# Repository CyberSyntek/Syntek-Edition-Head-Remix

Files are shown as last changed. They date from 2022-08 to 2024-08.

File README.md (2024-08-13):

Welcome to the Syntek Edition Head Remix!
=
TempMainSnip

UPDATES / NOTES
= 

Some of the information on this page is very outdated! I had originally designed the project to work with MG90D sized servos and a PCA9685, which was later changed to using the recommended setup as listed in the BOM. 

Due to the changes over time, the tutorials maybe a bit clunky in that respect as alot of the pictures used still include the old servos and PCA9685. Sorry about that. 

All the files you need are available though. :)

I'm currently using the JX Servo edit files of this head which will use the following servos to replace MG90D/MG92B. 

- x12 - JX PDI-1109

- x3 - JX PDI-1181

The PDI-1181 is a slightly larger servo so it will have more torque on all 3 jaw motors. The JX servos seem to be the quietest, no buzz and better performance servos out of the 7 different micro servos I bought and tested. They should really improve overall performance in general. 

I have left the files to use the previous old setup available also for those wishing to use MG90D/MG90S type servos.

I likely will not be updating this page further or do not have plans to do so at this point. I am planning on working on a more advanced silicone cast type head at some point in the future which is where the focus will be directed. 

ABOUT
=
On this page you will find all of the Syntek edition remixed head stl files, components needed, step by step put together tutorials and information relating to getting it running in myrobotlab (MRL). Future updates and files shall be available here as well. :)

As I am still early into the experimenting phase of this head also, I expect that there will be a number of updates to improve this page, files and write ups in the weeks to come. Stay tuned!

WHAT IS SYNTEK?
=
An introduction to Syntek (My InMoov Robot)

https://user-images.githubusercontent.com/81597534/182945941-7be97dca-e8e5-45d9-b666-c8eca6ea6b64.mp4

CURIOUS ABOUT INMOOV?
= 
If you were unfamiliar with InMoov robot and or are now more curious about it, you should head over to the InMoov website and find out more about the project  by clicking the image below as THIS project page is directly related to the InMoov project. 

<a href="https://www.inmoov.fr" />


WHAT IS THE SYNTEK EDITION REMIXED HEAD?
= 
It is a mostly magnetically held remixed edition of Gael Langevin (InMoov Founder)'s InMoov robot head that has been fit with independent eyes, eyelids, eyebrows and an additional axis in the jaw. This head is controlled via a PCA9685 micro controller, an Arduino Nano and MYROBOTLAB and can be built to function independently or as part of your InMoov robot. 

FIRST TIME USING A PCA9865 AND MYROBOTLAB?
=
No problem! Here is my "Beginners guide to moving servos with a PCA9685 and MYROBOTLAB" video to help you get started.

Beginners guide to moving servos with a PCA9685 and MYROBOTLAB (https://youtu.be/unIUJA24uBI  "Beginners guide to moving servos with a PCA9685 and MYROBOTLAB")

And while we are at it, here is a bonus link to the MYROBOTLAB (MRL) homepage: http://myrobotlab.org/

-BOM- 
=
For a full detailed list of the electronics, hardware and everything needed, please refer to BOM readme file. 

https://github.com/CyberSyntek/Syntek-Edition-Head-Remix/tree/main/BOM

TUTORIALS
= 
The tutorials begin here!

https://github.com/CyberSyntek/Syntek-Edition-Head-Remix/tree/main/01-MainPlate

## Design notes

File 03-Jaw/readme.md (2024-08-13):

JAW - STL FILES
=
JawFiles

WARNING: Some of the files may look different than the original tutorial as they have been updated and adjusted to meet other changes in the build so far. I will update the images to match the parts eventually. The put together is still the same, just slightly altered a few parts for better functionality.

- ServoConnector-JXedit.stl x2 - IF USING RECOMMENDED SERVOS FROM BOM, PRINT THIS!

- ServoConnectorV2 - x2  - If using the above, you do not need to print these. These were for original MG90D servo builds.

- BallLinkConnector

- Hinge-L

- Hinge-R

- HingeBase

- HingeCover

- HingeLink

- Jaw - (V2 Jaw modified to fit AdjustableInsert.stl from the skull page. 

ELECTRONICS
=

- x2 - JX PDI-1181 servos. (Lateral Jaw). 

SCREWS / BOLTS / CONNECTORS
=
- x4 - M2x8mm Screws 

- x4 - M2x12mm Screws

- x4 - M2x8mm Bolts

- x2 - M2x16mm Bolts 

- x2 - M2x20mm Bolts 

- x6 - M2 Nuts

- x4 - Servo Screws

- x8 - M3x12 Bolts 

- x4 - M3x16mm Bolts

- x2 - Zipties

- x2 - 2-56 or M2 Threaded Ball Links

TUTORIAL
= 
We will prepare a few of the individual parts before we attach them all together in the next 3 steps.

L&R Hinges to Jaw
=
Screw in x4 M3x12mm Bolts to connect both side Hinges to the Jaw. This area can be tight on a screw driver, but you should be able to manage with playing the angles.

00-Jaw

HingeLink Prep
=
Screw in the Ball Joint piece from either a 2-56 or M2 Threaded Ball Link into the HingeLink until it sits flush.

02-HingeLink

BallLinkConnector Prep
=

Take x2 M2x20mm Bolts and cut the bolt heads off of them. Screw in the bolt rod pieces into the x2 Threaded Ball Link pieces as seen in image. Screw those into each side of the BallLinkConnector.stl file and make sure that the empty ball joints are both facing the same direction. We will be putting this piece aside until the "03-BrowPlate" tutorial. Keep it and the remaining x1 ball joint in a safe place until ready to use it! 

BallLinkConnector

HingeBase to ServoConnectors
=

Note: The servoconnectors are now ServoConnectorsV2 and will appear different. See "Lateral Jaw Servo Horns" below for the updated image. 

First we will insert x2 M2 Nuts into the HingeBase. Ideally we will use a little bit of superglue to keep it held in. Next we will line up the Servo Connectors with the HingeBase and screw in a Mx16 Bolt through to the M2 Nuts. You want the ServoConnectors to still be able to swing around freely so make sure not to over tighten them. Just enough that there is no play between the HingeBase and ServoConnectors. You may also wish to carefully apply a little drop of the on the tip of the bolt where it is connected to the nut so that it doesn't slip over time.

01-HingeBase

Assemble the Above
=

Now we will attach all of the above parts we just prepared. You should be able to manage to get the HingeBase into the circular slots on the Hinges at this point without much trouble. When inserting it make sure that the side with the M2 Nuts is facing the top. 

Slide the HingeLink between the Hinges with the Ball Joint on the top side and screw in x4 M2x12mm Screws so that everything is held together.

03-JawAssembly

HingeCover to Jaw
= 

Flip the Jaw over and screw the HingeCover on using x4 M2x8mm Screws. This HingeCover is completely optional and was made to avoid the hollow mouth look.

04-HingeCover

Lateral Jaw Servo Selection
=
We need two servos with similar servo spline to servo horn orientations as we will be running these servos with a Y cable through a single pin on the same signal. Make sure that both of your servos are able to hit the same servo horn position for both servos or try swapping out some different servo horns on the servos until you can find a good matching set. 

Y-Cable
= 
You will want a Y cable such as this one or you can make your own with some servo extension cables. Make sure to test the servos running together and that they are moving in sync and to the expected positions. 

YCable

Lateral Jaw Servos and Cutting the Tips
=

05-ServoAndTips

Lateral Jaw Servo Horns
=
We will be screwing in x4 M2x8mm bolts from the top side of the servo horn into the ServoConnectors which are now fit with x2 M2 nuts on the bottom sides. 
The bolts will be inserted into the 2nd and 5th from the center of the servo horn holes as seen below.

V2ServoConnector

Zip Ties
=

You will want to attach a ziptie around each of the current jaw servos that we have attached so far. First begin by running the servo cable along the inside open area beside the servo. Tighten a ziptie around the servo and push it downwards so hold the servo cable in place. The ziptie should also be able to slide down into the openings on both sides of the servo. The reason for this is that we want the cables running towards the front and staying away from the back as we will later have a gear for the neck located close by and we don't want our cables to get caught and chewed up in it. 
Zip

You will likely need to disconnect the servos from the Y cable to be able to get the wires through the following (03-BrowPlate) steps, so keep it somewhere safe after you have tested the servos working together.

Neck & Cable Planning
=
It is right around this stage that you want to begin to plan what you are going to be attaching the head to and what preparation needs to be done as far as the cables you will be needing to run through the neck. Regardless if you are using the a head stand or attaching it directly to your InMoov's body, it will be much easier to get your cables ready and through whichever neck you decide to use at this stage in the build before we add even more into the head.

If you are following the same set up as myself then you will see below that I am currently running a total of x4 cables through the neck and Maingear.
 
- +/- cables which will connect to the PCA9685's terminal block to power the servo motors.

- 3ft Mini B USB cable to power the Arduino Nano. (3ft)

  Note: The default cable that came with the nano was too short with the BackSkull attached.

- Micro USB to power the Raspberry Pi Zero W

Cableplanning

Once you have your cables through, you will want to reattach the MainGear to the MainPlate with the GearRing from the parts that we printed earlier in the MainPlate section using the x4 M3x12mm Bolts.

NeckMainGear

You will want to attach the MainGear to the NeckPlateHigh file from the InMoov website using x4 M3x16mm Bolts screwing them in from the inside of the NeckPlateHigh. 

NeckPlateHigh

Download the NeckPlateHighV2.stl file from here. http://inmoov.fr/inmoov-stl-parts-viewer/?bodyparts=Neck

At the time of writing this, I still am using Jon Bailey's headstand and have yet to move to my Inmoov's body. Number of cables through the neck may increase as parts get further updated. 

You can download Jon Bailey's Headstand from here - https://www.thingiverse.com/thing:4670770

Bad Hair Day
=
If you have followed along so far and are using John Bailey's headstand then your build should look just like this. A BAD HAIR (wire) DAY!

BadHairDays

YOUR JAW IS FINISHED!
=
Now we can move onto the 04-BrowPlate readme file for the following tutorial.

https://github.com/CyberSyntek/Syntek-Edition-Head-Remix/tree/main/04-BrowPlate

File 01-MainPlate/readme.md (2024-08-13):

MainPlate - STL FILES
=
MainPlate

- MainPlate-JXedit.stl  (If using JX PDI-1181 servos)

NOTE: MainPlate-JXedit.stl is recommended to use instead of MainPlate.stl as it uses the more current servo set up.

- MainPlate.stl (Out dated - Was made for micro servos such as MG90D or MG92B) - I'll leave here as an option. 

- BaseConnector.stl - x12

- MainGear.stl  

  Note: This maingear is a very slightly altered version of Ray Edgley's custom MainGear file"

- GearRing.stl

- CamCableClip.stl - x2 (x4 if using two cameras.) 

MAINPLATE PREP 
=
This video will help you prepare the MainPlate and the included neck files. 

https://user-images.githubusercontent.com/81597534/183753533-ba753258-47c7-4725-9bed-b562950ec410.mp4

Note: The MainPlate.stl has been further adjusted since this video and may look slightly different. The clean up prep method and suggested methods remain the same with the current version. 

I suggest waiting to apply the grease to the MainGear as mentioned in the above video until you reach the "03-Jaw" folder tutorial in the readme file as the grease can get a bit messy. 

You will want them printed now to prepare and make sure everything fits well and will be reattaching them later on. 

Before you begin to print everything off, I suggest that you check the below video for the recommended calibration settings.

GETTING CALIBRATED / POTENTIAL NECK OPTIONS
=
https://user-images.githubusercontent.com/81597534/183754601-2d7bb311-81e5-410d-bdfd-17bd113c6ecd.mp4

This should give you an idea on how you want your slicer calibrated for printing if you have any issues. I would suggest printing the Calibrator file from the InMoov website before you begin printing everything off. I've also included a potential neck option that you may want to use for your head project, or atleast until you are ready to get it onto the body of your robot. 

InMoov Calibrator - <a href="https://inmoov.fr/wp-content/uploads/2019/01/Calibrator.stl">Calibrator.stl</a>

Jon Bailey's Head Stand - https://www.thingiverse.com/thing:4670770

CONTINUE TUTORIAL
=
The tutorial for the MainPlate files will begin in the "02-Eyes" folder readme file.

https://github.com/CyberSyntek/Syntek-Edition-Head-Remix/tree/main/02-Eyes

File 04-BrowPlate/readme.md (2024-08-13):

BROWPLATE- STL FILES
=
BrowPlatePieces

- BrowPlate-JXedit.stl (THIS IS THE MOST UPTO DATE AND USES THE RECOMMENDED SERVOS FROM THE BOM!)

I suggest using the file above with the recommended servos instead, but I will leave the prior version so the option is still open.

- BrowPlate.stl (If using MG90D sized servos)

- BrowHolderL-V1.stl

- BrowHolderR-V1.stl

- MagnetHolder.stl x4

- NanoHolder-A.stl

- NanoHolder-B.stl

- PCA9685Mount.stl

- PCA9685MountSupport.stl x4

- TPUBrow-L-V1.stl (MADE FOR TPU)

- TPUBrow-R-V1.stl (MADE FOR TPU)

ELECTRONICS
=
For more detailed information on electronics & hardware needed, please refer to the BOM folder readme file.

https://github.com/CyberSyntek/Syntek-Edition-Head-Remix/tree/main/BOM

- x4 - JX PDI-1109 Servos.

- x1 - JX PDI-1181 Servo. 

- MPU6050 (Currenly optional. It is slotted on the BrowPlate if wanting to experiment.)

- Raspi Zero W

SCREWS / BOLTS / CONNECTORS
=
- x6  - M2x5mm Screws

- x6  - M2x7mm Screws + x2 - If a second "Rasberry Pi Zero W"

- x8  - M2x8mm Screws

- x10 - M2x16mm Screws

- x10 - Servo Screws

- x4 - Du-Bro E-Z Connectors With Re-Usable Nylon Snap Ons

MAGNETS
=
- x4 - 10x3mm Neodymium Magnets
 
- x4 - 6x3mm Neodymium Magnets

  Note: Info on BOM

OTHER
=
- x4 - Strands of either ABS or PETG filament Filament

- Superglue

- TPU to print eyebrow files. 

TUTORIAL
= 
SERVO PREP - Ball Joint
=
Set servo to 90°/centered. We will want to drill the 5th from the center hole on the servo horn to be able to screw in the remaining Ball Joint we had left over from the 03-Jaw tutorial. With the Ball Joint now attached, attach the servo horn as shown in the image with the horn facing away from the wires. 

0001-BallJointPrep

Servo to BrowPlate + (MPU6050)
=
We will want to screw the servo to the brow plate with x2 Servo Screws as shown below with the servo horn facing towards the back. If you decide you will be using a MPU6050, it will be easiest to install it at this point also using x2 M2x5mm Screws.

0002-ServoMPU6050

Arduino Nano Mounts (NanoHolders)
= 
Screw on NanoHolder-A and NanoHolder-B to the BrowPlate using x4 M2x7mm Screws. The Arduino Nano should be able to click in at any point so you can either put it now or later. 

0003-NanoHolders

PCA9685MountSupports to BrowPlate
=
Screw in the x4 PCA9685MountSupports from the bottom side of the BrowPlate using x4 M2x8mm Screws

0004-PCA9685MountSupports

Attaching the PCA9685 and PCA9685Mount
=
Screw on the PCA9685Mount to the PCA9685MountSupports using x4 M2x8mm Screws followed by screwing on your PCA9685 to the PCA9685Mount using x4 M2x5mm Screws.

0005-PCA9685Mount

Brow Servos
=
Mount x4 Servos onto the BrowPlate using x8 Servo Screws.

BrowServos

Servo Horn Prep
=
We are going to want to attach our EZ connectors to the appropriate servo horns for each servo in this step. You will want to drill the holes in the servo horn wide enough to be able to push the EZ connectors through so that they can rotate easily enough and not be too stiff. Once through you will push on the nylon snap connectors so they are secured to the servo horns. With the servos all set to 90° / center you will want to attach the prepared servo horns to the correct servos as seen below. Inner Brow servos horns Inwards (5th from center holes) , OuterBrow servo horns facing outwards. (6th from center holes) 

BrowHornPrep

BrowHolders
=
Screw on the BrowHolder-L & BrowHolder-R using x3 M2x16mm Screws each. (x2 should be fine)

0007-BrowHolders

Attaching BallLinkConnector
=
You will now want to snap on the BallLinkConnector to the Ball Link on the servo so that it is hanging through the BrowPlate.

0008-BallLinkConnector

Attaching the BrowPlate
=
Attach the BrowPlate to the BaseBeams using x6  M2x16mm Screws. Now lift the jaw to within range to snap on the connector. You may need to move the servo horn downwards to allow yourself enough space to be able to snap it on by hand.  

0009-BrowPlate

Arduino Nano to PCA9685
=
Now to connect the Arduino Nano to the PCA9685 using 4 dupont cables.

0010-NanoWires

Progress Check
=
At this stage the head should be looking like a bad hair day. If yours resembles this then we are good to move on. 

ProgressCheck

Servo Cables to PCA9685
=
Now want to begin connecting the servo wires to the PCA9685.

On the PCA9685Mount file you will see the open area on the left side highlighted in the red circle. We will want to slide the following servo cables through that area. You should be able to fit them all in withough too much trouble. The last one or two can get a bit tight so give other cables slack as needed to help them be able to slide up. 

0011-CableSlot

- LateralJaw - (Left side cable) This will be joined by the right side cable with the Y cable once through the slot.

- Jaw

- RightInnerBrow

- RightOuterBrow

- LeftInnerBrow

- LeftOuterBrow

- LeftLowerLid

- LeftUpperLid

- LeftEyeUD

- LeftEyeLR

With all your servo cables now plugged in you should only have Pin 0 and Pin 9 open on the PCA9685. On the right side your servo cables will still be loosely hanging off to the side as seen above. 

Raspberry Pi Zero W Prep
=
Now we will connect the eye's pupil camera cable to the Raspberry Pi Zero W.

RaspiConnected

We will want to take care of those loose wires now and try and push them into the opening seen below. Grab your Raspberry Pi Zero W and screw it in using x2 M2x7mm Screws which will hold the wires in place. If you have your camera placed in the left eye or are not using a camera at all, you can use zipties between the PCA9685MountSupports to hold the cables in place.

0012-RaspiZeroW

You may wish to unplug a few of the right side servo wires one at a time (Unless you labeled your cables) and wrap them around the other plugged in wires to reduce wire slack as some of them can get close to the eyebrow servo EZ connectors and could potentially get snagged. Obviously plug back in anything you unplug following doing so. :)

Getting Wired
=
Now we can plug in cables we had routed through the neck earlier. At the time of writting this, I am so far only needing to connect GND/V+, Mini B USB and a Micro USB.

0013-GettingConnected

Now plug everything in and confirm that everything works.

0015-Plugin

WORD OF WARNING
=
https://user-images.githubusercontent.com/81597534/184579363-48b3a739-7e1d-4e5d-9d5e-3c093b12aab9.mp4

Magnet Holder Prep 
=
To prepare the magnet holders you will need to get cut a few strands of PETG or ABS filament. The length doesn't really matter at this stage beyond being too short so give yourself a few inches to work with. You will want to slide the filament pieces into the MagnetHolders so that the filament curves away from the MagnetHolder pieces as seen in the image below. You will then want to apply a single drop of super glue into the Magnet holders and push the magnet in so that it is all the way in and flat. (Check to make sure your magnets fit okay prior to applying glue) There is a likely chance that some of the glue has worked its way through the bottom of the MagnetHolder into the shaft where the filament is inserted while pushing down on the magnet, but just make sure they don't easily fall out otherwise you may need to apply a tiny drop of super glue at the top of the MagnetHolder to keep the filament in place. 

0016-Magholders

Alternatively you don't need to use filament on these as there are other options out there, this just seemed like a cheap way to use something we already have. You can also use something like GoldenRod/GoldenWire for RC airplanes here that comes in various stiffnesses and widths or perhaps some kind of instrument wires. (I haven't tried yet) Whatever is used needs to be stiff enough that it will still be able to push, but flexible enough to bend through the MagnetHolders. 

Here is an example of the length which you will likely want to aim for that will allow you a little bit of room still to play with adjustments.

MagHoldLength

Setting the Brows Limits
=
Before we connect the MagnetHolders we prepared we will need to set our Eyebrow servo limits. If you are using my MRL-Files config you will see that I have them currently set between a Min:40 (Brows Down) / Max:140 (Brows Up) range. We will want to move the servos into their Max/Up position.

Browset01

Loosen the screws at the top of the EZ connectors so that you are able to slide the filament into them. Push the filament all the way through until the top of the MagnetHolder is pressed against the MagnetHolder. You will want to adjust the filament so they magnets are facing mostly forwards but with a slight angle towards the direction needed. Left brows > Slight left angle. 

Double check them to make sure they are all leveled the same and then finally tighten the EZ connector screws so that they are locked into position.

0017-BrowSet

EyeBrow Prep
=
Take x4 6x3mm neodymium magnets and place them on the MagnetHolder magnets. At this time it is a good idea to mark them with a marker so that we know the polarity of the magnets. One at a time, remove the magnets and with the marked side of the magnet facing towards the prints, glue the magnets into the TPUeyebrows using a single drop of super glue and repeat this step for all four magnets. 

Mag0001

BADTPUMagnet

We will put these aside for the moment until we have completed the next steps.

BROWPLATE IS FINISHED!
=
Now onto the final step located in the 05-BrowPlate folder readme file.

https://github.com/CyberSyntek/Syntek-Edition-Head-Remix/tree/main/05-Skull

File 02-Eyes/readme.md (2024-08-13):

Eyesexample

ABOUT
=

The eye mechanism is a direct remix of Will Cogley's "Compact Animatronic Eye Mechanism" in which I have seperate both sides of the eyes to be independent mechanisms, modified to use independent eyelids, fit the eyeballs with cameras and reworked to allow for it to fit inside of the Syntek Edition InMoov skull. (Plus a few other changes.)

This mechanism could not have been done without the hard work of Will Cogley putting together his original eye mech. I would like to send out a huge thank you to Will for his hard work and for giving me permission to post the remixed files for others to use. Thanks Will!

NOTE: This eye mechanism is still compatible with Will's original eyes. You can head over to his site and download his eye files there if you are not planning on using cameras in your build. He also has various videos on his youtube channel relating to eye mechanisms and how to make realistic looking eyes as well as a resin cast kit for his original eyes with the files for those available on his website. 

Will Cogley's Website: www.nilheim.co.uk/

Here is a link to Will Cogley's "How to Make a Compact Animatronic Eye Mechanism with 3D Printing and Arduino" video. Give it a watch through as it may help as a reference for various things relating to this eye mechanism as well. https://youtu.be/ihXxbQefl1c

RIGHT EYE - STL FILES
=
You will need the following files for both the Left and Right eyes. Example: L-Base.stl & R-Base.stl located in the folders above.

EyepartsDisplay

- Base.stl (If using JX PDI-1109, please print Base-JXedit.stl instead.)

- BaseBeam.stl x3

- BaseExtension.stl

- BottomEyelid.stl

- BottomEyelidConnector.stl

- EyeAdaptor.stl

- Eyeball-Cam1Fit.stl  (Requires Supports)

- Eyeball-Cam1Fit-Design1.stl (Requires Supports) This is the same version as the file above with a design cut into it.

- Eyeball-Cam2Fit.stl  (Requires Supports) - This is for a different camera. Info will be listed soon. 

- Eyeball-Cam2Fit-Design1.stl (Requires Supports) This is the same version as the file above with a design cut into it.

- EyeHolder.stl (If using JX PDI-1109, please print EyeHolder-JXedit.stl instead.)

- EyelidHolder.stl 

- EyeLink.stl x2

- MainPivot.stl (Supports can help)

- RasCamModuleHolder.stl

- ServoHolder.stl (If using JX PDI-1109, please print ServoHolder-JXedit.stl instead.)

- SmallPivot.stl (Supports can help)

- TopEyelid.stl

- TopEyelidConnector.stl

ELECTRONICS (PER EYE)
=
For more detailed information on electronics & hardware needed, please refer to the BOM folder readme file.

https://github.com/CyberSyntek/Syntek-Edition-Head-Remix/tree/main/BOM

- x8 - Micro Servos. / x4 per eye. (ATTENTION: Originally I was using MG90D servos, later moved to using JX PDI-1109 servos.) 

Please print according to which servos you are using. 

  EXAMPLE: If using "JX PDI-1109" you will print "Base-JXedit.stl" /// If using "MG90D", print "Base.stl".

  NOTE: It is possible to put cameras in both eyes, but you really only need one.

- x1 - 8MP Camera Module 77.6° Wide Angle Field View Camera for Raspberry Pi

- x1 - Raspberry Pi Camera Module V2

- x1 - 11.8" (30cm) Raspberry Pi Zero Camera Ribbon Flex Extension Cable

SCREWS / BOLTS / ETC (PER EYE)
=

- x8 Servo Screws - Total Needed = x16

- x4 M2x6mm Screws - Total Needed = x8

- x9 M2x7mm Screws - Total Needed = x14 (x18 If double camera)

- x8 M2x8mm Screws - Total Needed = x16

- x3 M2x10mm Screws - Total Needed = x6

- x10 M2x12mm Screws - Total Needed = x20

- x3 M2x16mm Screws - Total Needed = x6

- x3 M2x6mm Bolt - Total Needed = x6

- x3 M2x7mm Bolt - Total Needed = x6

- x1 M2x9mm Bolt - Total Needed = x2

- x2 M2x28mm Bolt OR 25mm Threaded Rod - Total Needed = x4

- x2 Du-Bro 2-56 Swivel Ball Link Connectors OR M2 sized Swivel Ball Link Connectors   - Total Needed = x4

  #NOTE: I ordered a few batches of M2 connectors from various sellers, none of them were nearly as smooth as the Du-Bro connectors. 

TUTOTIAL (Right Eye)
=
Note: Start with one side (L-Eye or R-Eye) until you reach the "Single Unit Base" section of this tutorial.

BaseConnectors to MainPlate
= 
Take x6 BaseConnector pieces and slot them into the MainPlate for whichever side eye you decide to start with. Screw them together from the bottom side using x6 M2x8mm screws. I will be using the right side eye in these examples. 

001-BaseConnectorToMainPlate

Base to BaseConnectors
=
Place the Base on top of the BaseConnectors. Once the holes are lined up,screw them together with x6 M2-12mm screws.

002-BaseToBaseConnector

Gluing the BaseConnectors
=
Apply a drop of superglue to where Base and BaseConnector are now joined at the bottom of the Base. This will prevent the baseconnectors from being able to rotate. Give the glue a few minutes to dry and come back. 

Superglue1

#MORE GLUE!
=
Unscrew the x6 screws from the bottom of the Mainplate and remove the Base. Now you will be able to apply a bit more superglue with easier access to the bottom of the Base. After the glue dries you can either remove the x6 M2x12mm screws or leave them in, it doesn't really matter. (I leave them in for added strength.)

Superglue2

Single Unit Base
=
With the BaseConnectors superglued to the Base and locking them into place unable to rotate, we can now remove the Base as a single unit by simply removing the x6 screws on the bottom of the MainPlate and plug it back into the MainPlate BaseConnector slots when needing to do so. 

003-GluedEyeBase

#REPEAT THE ABOVE STEPS ON OPPOSITE EYE
=
Now you will need to repeat the steps above for the opposite side eye. Having these single unit pieces finished and out of the way will make things much easier as we keep progressing. We need to do them one at a time so we can apply the glue to the BaseConnectors more easily.

Eye Servo Setup
=
Now it is time to mount the L/R and U/D servos for the eye mechanisms. With your servos preset to 90° (centered) mount them as seen in the image below and screw them in using some servo screws. 

#Note: I used some standard size servo screws here to make sure they had a solid hold, but you should be able to use the servo screws that come with your servos.

The servo horns will be mounted facing towards the outsides of the mechanisms.

005-EyeServos

ServoHolder to Base & Eyelid Servo Setup
=
Slide your servo wires through the top holes on the ServoHolder. Screw the servos onto the ServoHolder using x2 Servo Screws then mount the ServoHolder onto the Base and screw it on using x3 M2x12mm screws. Now we will add the otherside x2 servo screws to secure the servos in place.

These servos will also be centered / set to 90° when mounted.

Finally we will add the servo horns onto the servos in the positions seen below. 

06-ServoHolderServosToBase

EyelidHolder to Base
=
Now we will screw on the Eyelid holder to the side of the Base using x3 M2x7mm screws.

07-EyelidHolder

BaseExtension to EyeHolder
=
Align and screw together the BaseExtension and the EyeHolder using a M2x12mm screw. Once you are sure it is lined up well, you may want to apply a drop of superglue to prevent it shifting as the servos move which could offset the eyes movement. 
08-BaseExtension

Eye Connectors
=
Here we will want to use ideally x2 25mm threaded rods to screw into the the x2 EyeLinks and then adding a drop of superglue to secure them in place.

You will then screw on a 2-56 or M2 swivel ball link connector onto each of the rods.

I strongly recommend doing both eye's rods at the time as it will be easier to make sure both eye's rods are identical in length when adjusting the swivel ball link connectors.

#NOTE: I used M2x28mm bolts and cut the heads off the bolt which came out close to 25mm. 

010-2-RodToEyeLink

THE DANGER ZONE!!!
=
The following three steps are nicknamed THE DANGER ZONE I, II & III. 

While they are not actually dangerous, it is easy to mess them up doing this the wrong way.  

We will be needing to apply a tiny bit of superglue to the ends of the bolts just to give them a little bit of extra hold due to it is possible for the bolts to come loose over time with the servos constantly moving around and rotating around them. This can be very tricky if not being careful and will likely result in needing to reprint a few pieces. Luckily they are small pieces, but it is nice to avoid needing to do that.  

WARNING: You do NOT want to apply a drop of superglue directly on them from above as the glue will sink in from around the screw and fuse the pieces that we need to rotate together!

The best method I have found to do this is to squeeze a drop of superglue out into the lid of the storage bottle, run the tip of the bottle (Or anything small and thin really) against that single drop and gently rub a very small amount around on the needed area located at the end of the bolts WITHOUT squeezing anymore superglue out. Rub, no squeeze!

Always do this with the end of the bolt facing downwards as gravity is your friend. Even as it is drying you will want to rotate the pieces a little bit just to make sure that no glue has worked its way through and it can still move freely.

EyeLink to SmallPivot (THE DANGER ZONE I)
=
Take an M2x6mm bolt and run it through the EyeLink into the Small pivot. You will want to tighten it enough that is can still rotate freely, but you want to avoid it having any play between the pieces that could cause potential offset in the eye movements. This is more easily achieved if using a flat bottom head bolt, but should be possible with most shaped M2 screws if careful.  

Once you are sure that there is little to no play and that the screw is tight enough, but can still move friction freely.... it is time to enter "THE DANGER ZONE". You will want apply a tiny bit of superglue to the end of the bolt showing through the top of the SmallPivot. 

SmallPivotRod000

EyeLink to MainPivot (THE DANGER ZONE II)
=
Screw the EyeLink to the MainPivot from the top using an M2x6mm screw. Flip it over and carefully enter "THE DANGER ZONE" again.

012-RodToMainPivot

EyeHolder to MainPivot (THE DANGER ZONE III)
=
Attach the EyeHolder to the middle of the MainPivot screwing in a M2x6mm bolt from the bottom. This one is the most dangerous, but you are almost there. Flip it over and defeat "THE DANGER ZONE" with a tiny bit of super glue. 

013-BaseExtensionToMainPivot

You Survived THE DANGER ZONE
=
You did it! That was the most difficult part of this project! Good job friend! :)

Pivots to EyeAdaptor
=
Slot the Small Pivot and MainPivot into the EyeAdaptor gently. 

014-RodsToEyeAdaptor

Eyeball to EyeAdaptor
=
While this step is not overly difficult it can be a little tricky so take your time. 

You will want to place your camera into the slot in the Eyeball and snake the camera cable through the open slot on the EyeAdaptor. As the Eyeball camera slot is not overly tight it is easy for the camera to come loose when trying to push the Eyeball onto the EyeAdaptor. Don't panic!

It is easiest to push the EyeBall onto the EyeAdaptor a little bit and slowly push it down. Even if the camera comes loose from its slot, you will be able to adjust it back into the slot by moving the cable around. The further you push the EyeAdaptor in the easier this becomes. The main thing to be careful of is that you are not pushing it in so far that you are crushing the camera if it isn't aligned or that it has become so tight that you cannot align it back into its slot by moving the camera's cable around easily as the cable is fragile. The EyeAdaptor will hold it in place once it is fully on, so just take it slow and try and align it closer to when the EyeAdaptor is getting closer to being fully inside the Eyeball. 

EyeballToEyeAdaptor

Screw Check
=
Make sure to check the bottom of the Base and see if any of the tips of the Servo Screws are sticking out. This will depend on which servo screws you use, but if any tips are sticking out then cut them off. Having the screws stick out here can damage your camera cable or less likely... your servo cables if you are unlucky. It is best to cut them flush with the bottom of the Base.

ScrewCheck

BaseExtension to Base
=
Align the BaseExtension on its slot on the Base and hold it in place with your finger. From the bottom of the Base you will want to line up the RasCamModuleHolder with the holes and run x3 M2x10mm screw threw both the RasCamModuleHolder and Base into the BaseExtension.

BaseExtensionToBase1

Eyeball - Servo Horns
=
Following the image below, you will want to attach swivel ball link connectors to the servo horns using x2 M2x8mm screw. The L/R eye servo horn hole you will be attaching the swivel ball link connector to is the 2nd from the center of the servo horn. The U/D servo horn hole will be the 4th from the center.

It is possible to do this stage before entering "THE DANGER ZONE" so that you can attach one or two of the swivel ball link connectors to make sure that the eye is facing forward directly without having any offsets and needing to unscrew the swivel ball link connector a bit until it lines up. They will all need to be the same length so it is possible to just connect one, remove it and adjust the rest of the rod lengths to match the one you know lines up well. 

Alternatively, even if you have completed "THE DANGER ZONE" you can screw it on, check for offsets, and unscrew the swivel ball link connector a bit with the rod still attached to the pivots with some care. Either way should be fine and will be your choice. 

EyeballServoHornHoles

Eyeball - Servo Check
=
Connect your servos and test your eyes using limited range Min/Max settings to make sure you do not have any strange movement occuring or offsets.

You can do this various ways such as using a servo tester or by running them in MRL. I have given examples of my servo limits in the MRL-Files section. Trust me, it is better to do now than later, I know from experience. :)

Eyelids 
=
Now that you have confirmed your eye works without issue and there is no offsets, it is time to move onto the Eyelids.

Before we install the eyelids onto the mechanism, I would recommend that you check your eyelids can close to a flush position. This will very much depend on your print settings and if little obstructions in the print will prevent them from closing all the way or not. This may not be needed, but it is easiest to check now. 

Screw in some bolts into both sides of the eyelids so they are held together. Try closing them and check for any spaces between them. If they will not close all the way, hold them up against a light and check to see where they are being onbstructed from. Very often any obstruction in the printing will be close to the corners on both sides of the eyelids on both the Top and Bottom eyelids. Having good light here will be the key to see where the issue is. 

You can use a small file or sand paper to very lightly rub those areas with the bolts still in the eyelids and check them again. You will not need to do much sanding/filing here so go slowly until you are happy enough with the results assuming you even have any obstructions. :)

Now you are ready to get them onto the mechanism!

Eyelid-prep

You will want slightly screw in a M2x7mm bolt from the Base side, just enough so that it can grip the LowerEyelid. Next, slightly screw in a M2x9mm bolt from the EyelidHolder side so that it also grips the LowerEyelid. Now hold the TopEyelid in place and slowly tighten each sides bolts a little bit to that the eyelids are able to hang in place. Now that you have your hands free you can go ahead and carefully tighten the M2x7 bolt all the way (If you used a bottom side flatheaded bolt). Remeber that this is a pretty thin part so be sure not to over tighten or you may risk cracking it. 

The EyelidHolder side you will not have to tighten all the way if using an Mx9mm bolt. A M2x8mm bolt may also work, although I wanted to avoid the risk of the Eyelids coming loose from the screw for less troubleshooting. Just make sure it is screwed in enough to hold the eyelids, but not rub against the eye with the eye turning L/R. 

You can now take the TopEyeLidConnector (shorter) and attach it to the TopEyelid using an M2x7mm bolt. Next the BottomEyelidConnector (longer) will be attached to the BottomEyelid using another M2x7mm bolt.

Now you can attach the corresponding EyelidConnectors to the top and bottom servo horns using M2x7mm screws into the 6th hole from the center holes of the servo horns as seen in the image below.

You may want to test the Eyelid servos at this point just to make sure the Eyelid Connectors are holding to the Eyelids, nothing is too tight or too loose and that everything is moving okay as it will a more tricky to adjust things once we have everything attached.

Eyelids

BaseBeams to Base
=
Screw the x3 BaseBeams to the base using x3 M2x16mm Screws. You CAN superglue these also, but it isn't absolutely necessary. 

BaseBeams

Base returns to MainPlate
=
Our eyes are finally ready to come back home to the MainPlate. Screw them in again from the bottom of the MainPlate using the x6 M2x8mm Screws (per eye).

You will want to make sure to run both the U/D and the L/R servo cables inbetween the BaseConnectors located under the ServoHolder containing the Eyelid Servos as shown in the image below so that they run off to the side.

EyeCables

Once the eyes are back on, flip the MainPlate over and screw on the CamCableClips for whichever side you are using a camera. 

#Note: If using two cameras, obviously put CamCableClips on both sides. :)

CompleteEyes

Note# Using some M2x7mm Screws, You may attach the Raspberry Pi Camera V2 Module to the RasCamModuleHolder now or later on when we attach the Raspberry Pi Zero W in the "04-BrowPlate" folder tutorial. 

To ensure the camera cables stay in the best condition until we attach them, I would suggest waiting unless you have everything ready to mount it to a headstand or your robot. 

You will need to attach the Raspi Zero W camera cable to the Module prior to mounting it to the RasCamModuleHolder and then sneak the cable through the CableClips as seen in the image below. The cable will come up and through the slot under the Eyelid servos. Once the cable is clear you can clip on the 8MP camera's cable onto the V2 Cam module.

CameraCable

NOW YOUR EYE MECHANISM IS FINISHED!
=
It is time to begin setting up the Jaw. This tutorial will be continued in the "03-Jaw" folder section page. 

https://github.com/CyberSyntek/Syntek-Edition-Head-Remix/tree/main/03-Jaw

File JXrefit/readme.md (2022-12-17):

These files are for the JX PDI-1109 x12 (small) and PDI-1181 x3 (larger) updated version of the head. 

I will need to update the github further and revamp the tutorials to use these files as they preform much better than the previous version which used MG90D.
The jaw required more torque to perform well and the PDI-1181 servos preform much better than MG90D/MG92B/etc tested so far.

These are the files I am currently using. 

The only thing I will mention is that on my current MainPlate the MainGear slot was a bit tight and I needed to sand it a little bit. I have expanded that by 0.20mm to hopefully overcome that, but I would need to reprint to know for sure. Maybe one of you can let me know how that works out. 

Note: Both eyes bases for the JXedits still use the same BaseExtension files uses in the eye file folders.

Example: R-BaseExtension.stl for R-Base-JXedit.stl / L-BaseExtension.stl for L-Base-JXedit.stl

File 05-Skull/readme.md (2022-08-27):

SKULL INFORMATION
=
The skull reshaping to allow for this to design to come together could not have happened without the wonderful help of Harry "Haracini". 

Random Note
=
You may have noticed in the pictures that my Eyebrows are leaving marks on my painted head. I still haven't painted it with a protective layer so that will happen hopefully this week and some photos will be updated. I am hoping that will do the job of preventing such things and I will update once I have repainted and given him a protective coat to confirm that will do the job. For those of you NOT painting, you have nothing to worry about. :)

STL FILES
= 
SkullPartsImage

WARNING: Some of the files may look different than the original tutorial as they have been updated and adjusted to meet other changes in the build so far. I will update the images to match the parts eventually. 

- FrontSkull.stl (Requires Supports)

- BackSkull.stl (Requires Supports)  Note: Printable as is, but I plan on making a more print friendly version eventually. 

- SkullCap.stl (Requires Supports)

- RotNeckGear.stl

  #Note: You will want to download some ears from the InMoov website. 
  
  http://inmoov.fr/inmoov-stl-parts-viewer/?bodyparts=Skull-and-Ears

  You MAY find other ear variations on www.thingiverse.com

SCREWS / BOLTS / CONNECTORS
=
- x8 - Servo Screws

- x2 - M4x16mm bolts. Note: I generally use slightly larger selftap screws on this for a stronger steady hold.

MAGNETS
= 
- x18 - 10x3mm Neodymium Magnets 

OTHER
=
- Superglue

TUTORIAL
=
IT IS FINALLY TIME TO HAVE A FACE!

MAGNET PREP
=
To start you will want to make x9 pairs of 10x3mm Neodymium Magnets and mark each side of each pairs back side with a marker. This way we will know the polarity of the set and which side will be inserted into the printer parts.
Magnets001

Checking the Slots
=
You will want to place the magnets into their slotted locations on the Front/Back and Cap of the skull to make sure that they can fit in easily and have enough room that they will be either flush with the part or slightly lower. If they are not you will want to file out the inner parts until they are so that you do not have any gaps in the skull pieces. 

Once you are sure everything is a nice fit, we will want to glue them into their slots with some superglue. As you can see my magnets on this first tester skull are not pretty as I used too much glue to make sure they would fit. You likely only need a single drop.

Flush001

Flush002

Attaching the RotNeck Servo
=
You will screw in the servo with x4 servo screws and the servo wire facing towards the left side of the skull. At this time you will have NOTHING attached to the servo side. We will want this servo set to 90° / Centered before we attach the RotNeck gear so either adjust it before attaching or after.

It can be a little tricky to get a screw driver in and around the magnet slots, but you should be able to manage. 

To prepare the RotNeckGear we will want to take the round servo horn with the screw that will attach it to the servo placed in the center of the servo horn and screw it to the RotNeckGear using x4 servo screws or similar sized screws. We will then line up the RotNeckGear and place it on the Servo. You will need a smaller screw driver like that which likely came with your 3d printer to be able to fit it into the center of the RotNeckGear and screw the servo horn to the servo.  

Finally you may wish to apply a little bit of grease to the RotNeckGear.

Servo0001

SettingServo001

ATTACHING THE BACKSKULL
=
You will want to angle the BackSkull onto the MainPlate and try and line up the RotNeckGear with the slot on the MainPlate as seen below.

BackSkull001

Hold the skull in place so that it is leveled and screw it into the MainPlate using x2 M4x16 bolts OR more recommended similar sized self-tapping screws so that it really has a secure grip. 

Hold001

You may find that it is hard to get the skull into a straight position and that the wires from your Raspi/Arduino/Power are getting in the way. I recommend that you give those cables enough slack that you can push the skull on and adjust the cables following having your BackSkull attached.

WireyStuff0001

Inspect around the RotNeckGear to make sure that there are no cables able to come in contact with it and potentially get stuck. 

WireCheck001

We will want to make sure that all the servo cables are behind the magnet slots so that the front skull will fit on without them getting stuck in between. This is the time when you may wish to apply a few more zipties to make sure your cables are clear and out of the way.

WireyStuff

ATTACHING THE FRONTSKULL
=
You will want to open the Jaw to its maximum range so that you have more room to work with while attaching the Front Skull. Woops! Make sure to check you don't have any eyebrows still on there!

WARNING: You will NEED to be very careful with getting around these bolts on both sides of the head. It is very tight, but with a slight flex of the skull and or some angling magic, you should be able to clear it without issue. I would suggest trying to clear one sides bolt one at a time until you manage and then it should go on easily from there.

Check to see that the magnets are all lined up and that the height looks to match with the eyes.

MaskOn001

Now you can attach the TPUbrows, close up his jaw and your head is finally all together. 

BrowsOn001

Congratulations! Your new head is now all put together and you are ready enter the wonderful world of playing with it and expanding it's functionality. 

CONTINUE YOUR JOURNEY?
=
You may wish to continue your journey over at the MRL-Files section of this page,

https://github.com/CyberSyntek/Syntek-Edition-Head-Remix/tree/main/MRL-Files

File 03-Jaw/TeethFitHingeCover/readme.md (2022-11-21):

These files are for if you want to add the lower teeth. After testing a little bit with them, due to the weight of the teeth there is a little bit of rattle so I may need to further alter them a bit eventually. 

So far I just stuck a little bit of silly putty on the underside of it to prevent any noise and it works fine.

I believe the screw size was M2x8mm from HingeCover to Teeth. 

These are optional files of course. :)

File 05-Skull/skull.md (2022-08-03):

SKULL INFORMATION

- FrontSkull (Requires Supports)
- BackSkull (Requires Supports)  Note: Printable as is, but I plan on making it more print friendly eventually. 
- SkullCap (Requires Supports)

The included "EarLeft" & "EarRight" are Gael Langevin's original ear designs from the inmoov website. 

Other ear variations are available on www.inmoov.fr and www.thingiverse.com

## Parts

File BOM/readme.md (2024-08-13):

RECOMMENDED SERVOS
=

You can likely use MG90S/MG90D/etc sized servos in place of the JX PDI-1109 servos without much issue.

JX PDI-1109 is still recommended as they are very slightly smaller, but more importantly, are quieter and sound less annoying. 

- JX PDI-1109 - x12

- JX PDI-1181 - x3

- x1 - DS3218 20KG Servo (270° ver) - https://a.co/d/8i4HSLo

RECOMMENDED SERVOS PER MECHANISM
= 
- Brows - x4 - JX PDI-1109

- Jaw - x1 - JX PDI-1181

- Lateral Jaw - x2 - JX PDI-1181

- Eyes/Eyelids - x8 - JX PDI-1109

- RotNeck - x1 - DS3218 20KG Servo (270° ver) 

TOTAL SCREWS (Self-Tapping)
=
- x6 - M2x5mm Screws

- x8 - M2x6mm Screws

- x20 - M2x7mm Screws

- x28 - M2x8mm Screws

- x6 - M2x10mm Screws

- x24 - M2x12mm Screws

- x16 - M2x16mm Screws

TOTAL BOLTS / NUTS
=
- x6 - M2x6mm Bolts

- x6 - M2x7mm Bolts

- x4 - M2x8mm Bolts

- x2 - M2x9mm Bolts

- x2 - M2x16mm Bolts

- x2 - M2x20mm Bolts

- x4 - M2x28mm Bolt OR 25mm Threaded Rod 

- x6 - M2 Nuts

- x8 - M3x12 Bolts

- x4 - M3x16mm Bolts

- x2 - M4x16mm bolts. Note: I generally use slightly larger selftap screws on this for a stronger steady hold.

- x2 - Zipties

TOTAL SERVO SCREWS
= 
- x38 - Servo Screws

OTHER HARDWARE
=

Links included are just for reference. If you can them find locally, cheaper or similar parts more easily, then please do so.

I likely won't be checking this page too often for expired links. 

- x4 - Du-Bro (2135) 2-56 x 1/2 Swivel Ball Link - https://a.co/d/0GZyHuL

  You can also use M2 Swivel Ball Links

- x2 - Du-Bro (181) 2-56 Threaded Ball Link - https://a.co/d/0wf1e1V

  You can also use M2 Threaded Ball Link.

- x4 - Du-Bro E-Z Connectors With Re-Usable Nylon Snap Ons - https://a.co/d/9076KMQ

- x1 - Y Servo Splitter Cable (Male to x2 Female) -  https://a.co/d/4Yzls2i

  You can make your own with some servo extension cables if unable to locate these. 

- x4 - Dupont Cables. (Arduino Nano to PCA9685) Perhaps a few more if MPU6050 is set up also.

- Krazy Glue/Super Glue (Please find locally for cheaper, but just incase) - https://a.co/d/6VbvxNa

- x2 - Zipties - You may find you want to use more to clean up the servo cables towards the end.

ELECTRONICS
=
WARNING: I have stopped using the PCA9685 and Arduino Nano on this project. You are still able to use them, but I would recommend against doing so.

- A power supply. (This may vary depending on how you are setting your head up/ If just head or head on body and more servos.)

The servos we are using are recommended to run at 6V. I would suggest using a 6V power supply or battery with as many amps as needed for your servos.

- Cables from power supply to terminal block on the PCA9685 to power the servo motors.   
  
- x1 - MPU6050 (OPTIONAL) - https://a.co/d/gO6KlX1 (There is a slot for one in the head, though I haven't experimented with it yet). 

IF USING PCA9685
=
- x1 - Arduino Nano (Brand or Generic)- https://a.co/d/9V0zZ5S  (I'm using generic without issue.)

- x1 - Mini B USB Cable (3FT) for the Arduino Nano - https://a.co/d/219j3qb

  If using either Jon Bailey's headstand set up (https://www.thingiverse.com/thing:4670770) or have the head attached to the body of your Inmoov (...I         think), 3FT should give you plenty of room to work with. The Mini B USB cable provided with the Arduino Nano will be too short. 

- Reason: PCA9685 seems to suffer from issues when applying speed reductions to your servos. / Servos jitter when running at slower speeds.  

- x1 - PCA9685 (16-Channel 12-bit PWM/Servo Driver) - https://a.co/d/cDNK8FY / https://www.adafruit.com/product/815

  These are available from various sellers, though the adafruit versions seem to be reliable. I'm not sure if the adafruit versions come included with components and or presoldered or not. I sourced my PCA9685 locally.

IF USING ARDUINO MEGA SENSOR SHIELD
= 

- Arduino Mega (Brand or Generic)

This is what I am currently using in place of the PCA9685. It is too large to fit inside the head, but does not have any of the above issues. 

- Arduino Mega Sensor Shield - https://www.keyestudio.com/products/free-shipping-keyestudio-mega-sensor-shield-v1-for-arduino-mega

These are also available on Amazon which is where I bought mine.

WARNING: If using this sensor shield, you MUST remove the jumper pin while powering the board with an external power supply. 

 SensorJumper

The Arduino mega will be USB powered, shield powered from your power supply. (Remove jumper as to not bridge both power supplies.)

PUPIL CAMERA RELATED ITEMS
=
PupilCam

Coming from the original Inmoov USB webcam pupil camera setup, I had decided I would stick with that route for my current pupil camera setup also by converting a Raspberry Pi Zero W into a webcam and using it in the same fashion. This isn't the most cost effective route for doing these things, but the size of the camera modules I found worked for the job. I am sure there are other options out there and I do plan on formatting the eyeball camera inserts for at least one other type of raspberry pi spy camera and will update those files here with a potential set up description when I have completed them. 

The following items are required for my current setup. 

- x1 - Raspberry Pi Zero W - https://a.co/d/f5wQHNF

  Raspberry Pi Zero and Zero 2 W may also work? I have never used or tried them, so use at own risk.  

- x1 - SD Card

- x1 - Micro USB cable (3ft) if not included with Raspberry Pi Zero W. 

- x1 - 8MP Camera Module for Raspberry Pi 77.6° Wide Angle Field View Camera Module for Raspberry Pi - https://a.co/d/1mauetZ 

  The link description says 5MP for some reason, but the cam cable has 8MP written on it as well as the comments confirming 8MP. These are available from various sellers. 

- x1 - Raspberry Pi Camera Module V2 - https://a.co/d/2dx2Vhr

  Make sure you are using the V2. Unfortunetly it is very difficult to find just these boards without a camera included as we will NOT be using the included camera due to needing a longer cable to be able to reach into the eyeball with enough cable slack to still function.

- x1 - 11.8" (30cm) Raspberry Pi Zero Camera Ribbon Flex Extension Cable - https://a.co/d/2RXyKAD

  We need a Raspberry Pi camera module > Raspberry Pi Zero camera cable.
  
===========================================================================

I recommend the following youtube video as a walkthrough for getting your Raspberry Pi Zero W's SD card formatted to function as a webcam. Her instructions are clear and the whole process takes about 2 minutes. 

"How to build a Raspberry Pi webcam | Easy beginner project!" - https://youtu.be/zmP1ZuV4kB8

The link she included in the video description is not the same as what she uses in the video. Here is the correct link to save you any headaches. https://github.com/showmewebcam/showmewebcam/tags

TOTAL NEODYMIUM MAGNETS
=
- x22 - Neodymium Magnets (10x3mm) - https://a.co/d/eTazw7q

- x4 - Neodymium Magnets (6x3mm) - https://a.co/d/bWqNBsL

I used the "NAZZO" brand of neodymium magnets found in the provided links as they are very strong and work well for our needs. I ordered two of the mixed sized packs as I was experimenting and wanted some size options to playu with. This is the link for the mixed pack I used. https://a.co/d/1fMVASk

Other options of that brand would be to get a pack of each of the sizes used if you are unable to source the needed neodymium magnet sizes needed locally.

- Neodymium Magnets (10x3mm) - https://a.co/d/eTazw7q

- Neodymium Magnets (6x3mm) - https://a.co/d/bWqNBsL

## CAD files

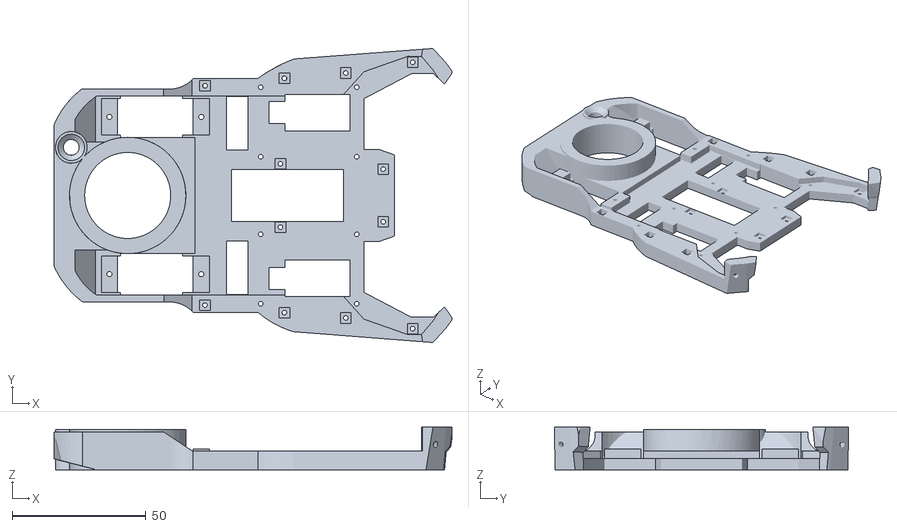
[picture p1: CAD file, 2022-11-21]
01-MainPlate/MainPlate-JXedit.stl
149.0 x 110.1 x 16.0

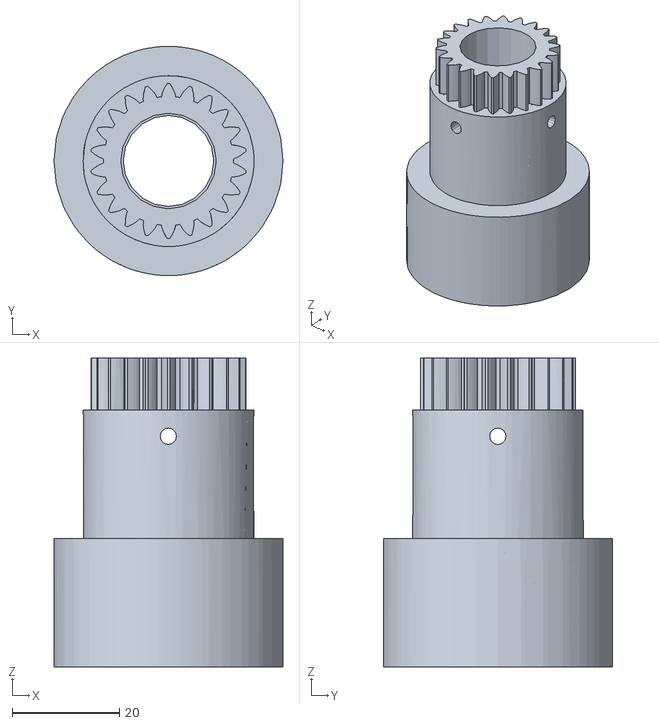
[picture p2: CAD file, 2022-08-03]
01-MainPlate/MainGear.stl
42.8 x 42.8 x 57.8

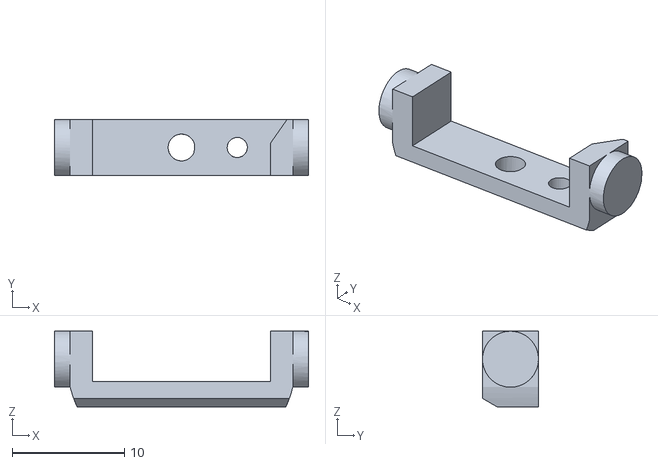
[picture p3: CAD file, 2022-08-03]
02-Eyes/LeftEye/L-MainPivot.stl
22.7 x 5.00 x 6.75

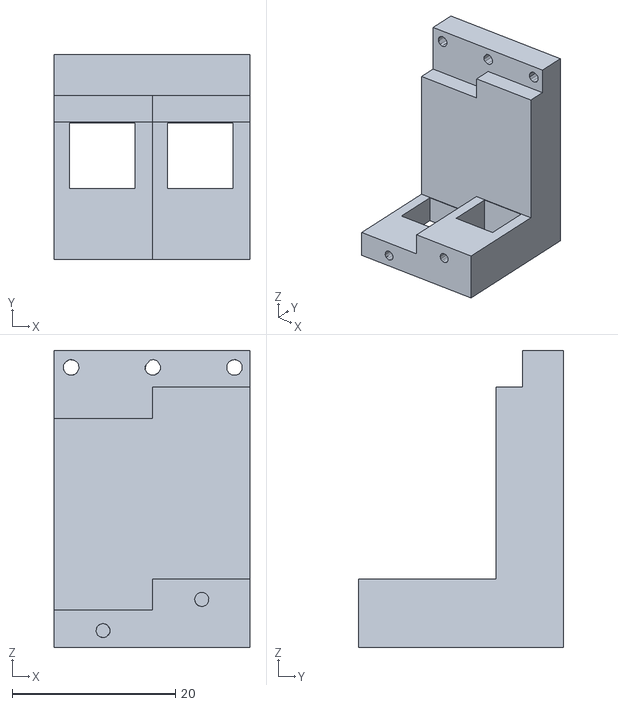
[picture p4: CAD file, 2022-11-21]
02-Eyes/LeftEye/L-ServoHolder-JXedit.stl
24.0 x 25.1 x 36.4

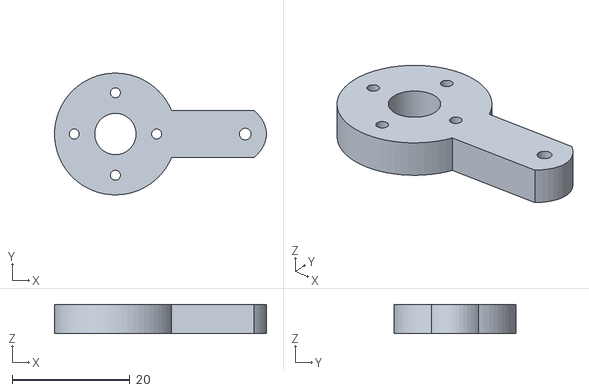
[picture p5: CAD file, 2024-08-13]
03-Jaw/ServoConnector-JXedit.stl
36.0 x 20.7 x 5.00

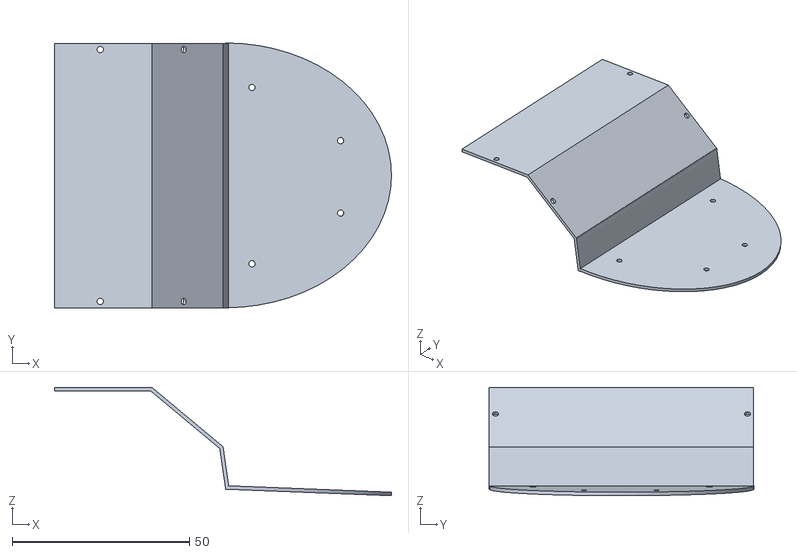
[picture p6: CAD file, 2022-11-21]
03-Jaw/TeethFitHingeCover/HingeCover-TeethFitV1.stl
95.0 x 74.7 x 30.6

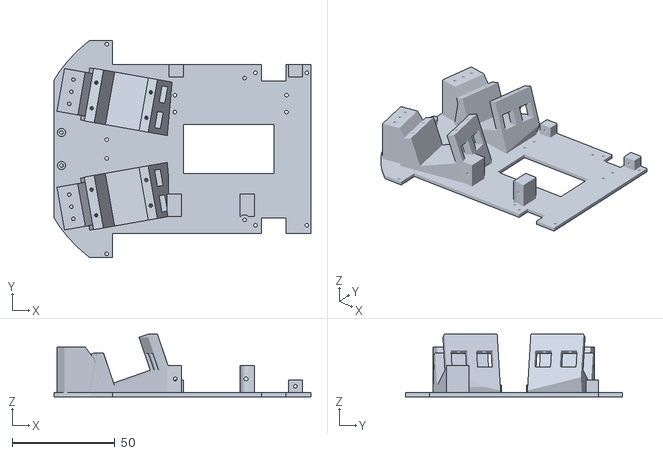
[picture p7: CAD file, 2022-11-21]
04-BrowPlate/BrowPlate-JXedit.stl
124.8 x 105.4 x 30.5

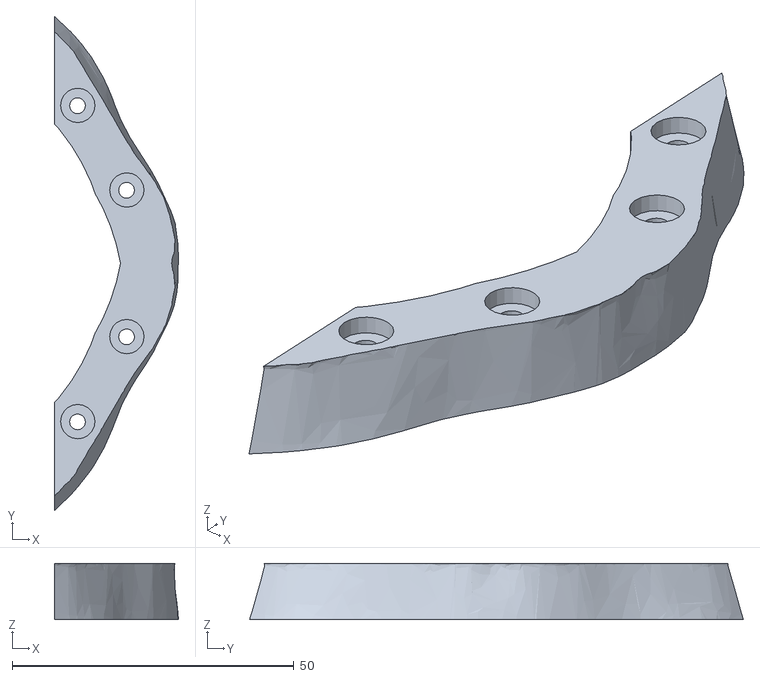
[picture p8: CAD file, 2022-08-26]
05-Skull/AdjustableInsert.stl
22.0 x 87.6 x 10.0

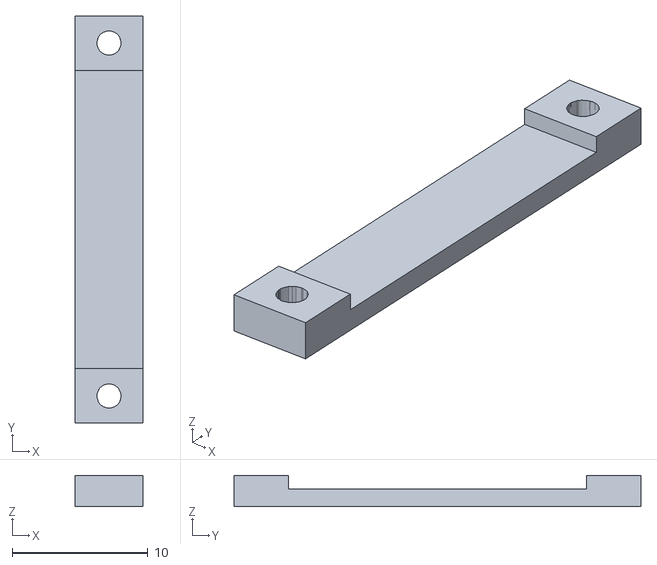
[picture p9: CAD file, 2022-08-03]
01-MainPlate/CamCableClip.stl
5.00 x 30.0 x 2.30

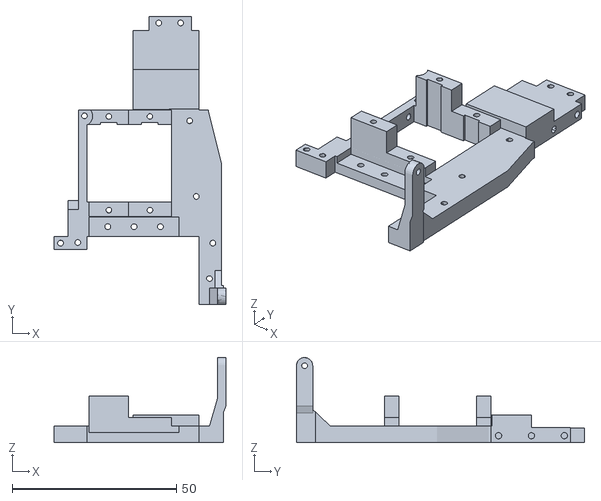
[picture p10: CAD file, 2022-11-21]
02-Eyes/LeftEye/L-Base-JXedit.stl
52.3 x 87.6 x 25.9

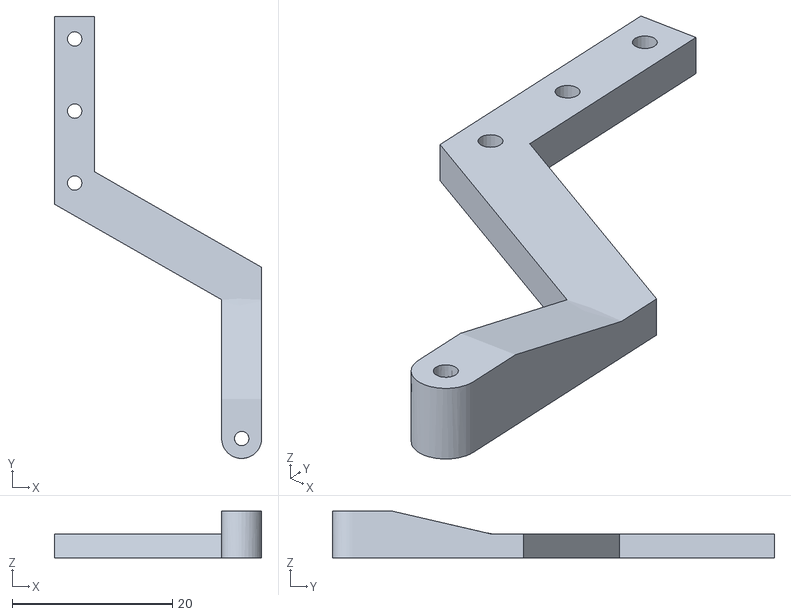
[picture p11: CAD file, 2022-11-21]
02-Eyes/RightEye/R-EyeHolder-JXedit.stl
25.9 x 55.2 x 5.85

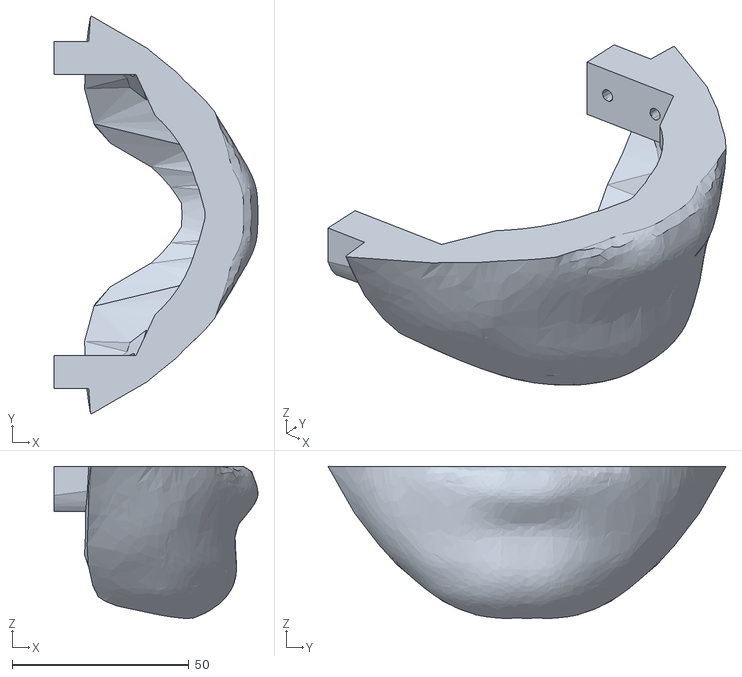
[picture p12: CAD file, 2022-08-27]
03-Jaw/JawV2.stl
57.7 x 112.7 x 43.1

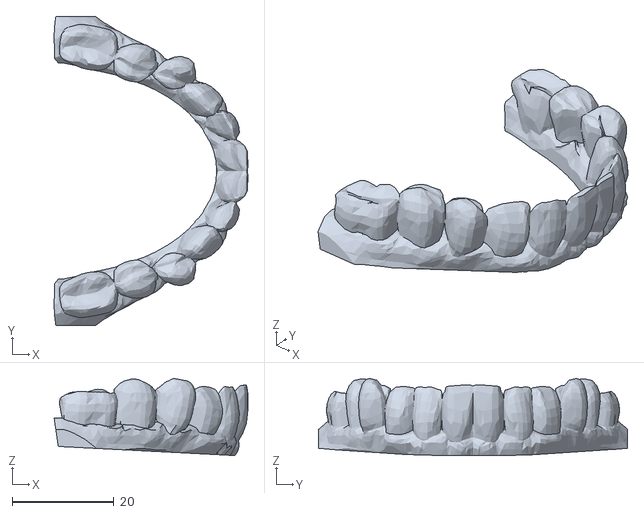
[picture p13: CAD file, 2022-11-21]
03-Jaw/TeethFitHingeCover/TeethV1.stl
38.2 x 60.8 x 15.2

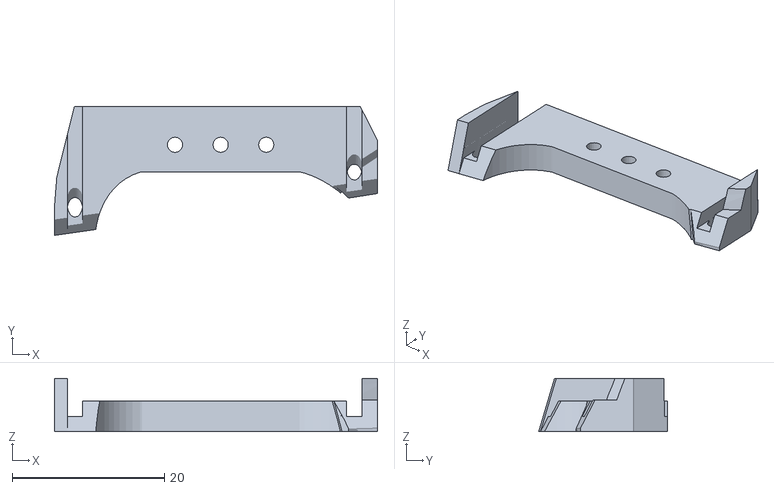
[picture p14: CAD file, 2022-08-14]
04-BrowPlate/BrowHolderL-V1.stl
42.5 x 16.9 x 7.00

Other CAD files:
01-MainPlate/MainPlate.stl
02-Eyes/RightEye/R-MainPivot.stl
02-Eyes/RightEye/R-ServoHolder-JXedit.stl
05-Skull/SkullCap.stl
01-MainPlate/BaseConnector-x12.stl
01-MainPlate/GearRing.stl
02-Eyes/LeftEye/L-Base.stl
02-Eyes/LeftEye/L-BaseBeam-x3.stl
02-Eyes/LeftEye/L-BaseExtension.stl
02-Eyes/LeftEye/L-BottomEyelid.stl
02-Eyes/LeftEye/L-BottomEyelidConnector.stl
02-Eyes/LeftEye/L-EyeAdaptor.stl
02-Eyes/LeftEye/L-EyeHolder-JXedit.stl
02-Eyes/LeftEye/L-EyeHolder.stl
02-Eyes/LeftEye/L-EyeLink-x2.stl
02-Eyes/LeftEye/L-Eyeball-Cam1Fit-Design1.stl
02-Eyes/LeftEye/L-Eyeball-Cam1Fit.stl
02-Eyes/LeftEye/L-Eyeball-Cam2Fit-Design1.stl
02-Eyes/LeftEye/L-Eyeball-Cam2Fit.stl
02-Eyes/LeftEye/L-EyelidHolder.stl
02-Eyes/LeftEye/L-RascamModuleHolder.stl
02-Eyes/LeftEye/L-ServoHolder.stl
02-Eyes/LeftEye/L-SmallPivot.stl
02-Eyes/LeftEye/L-TopEyelid.stl
02-Eyes/LeftEye/L-TopEyelidConnector.stl
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
